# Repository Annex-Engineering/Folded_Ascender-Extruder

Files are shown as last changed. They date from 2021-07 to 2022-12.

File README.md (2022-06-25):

# Double Folded Ascender Extruder - Release "4"

Folded Ascender is a take on the "popular" worm direct-driven extruder system. It is available in a 20:1 variant.

The original concept was originally developed by Trails and RentableSocks back in ~March 2019, it has since evolved many times and RentableSocks has now taken over development on this extruder full time.

Our discord server can be found here: 

Join me on Discord (https://discord.gg/MzTR3zE)

The BOM and Sourcing Guide for this product can be found here: https://docs.google.com/spreadsheets/d/1O3eyVuQ6M4F03MJSDs4Z71_XyNjXL5HFTZr1jsaAtRc/edit?usp=sharing

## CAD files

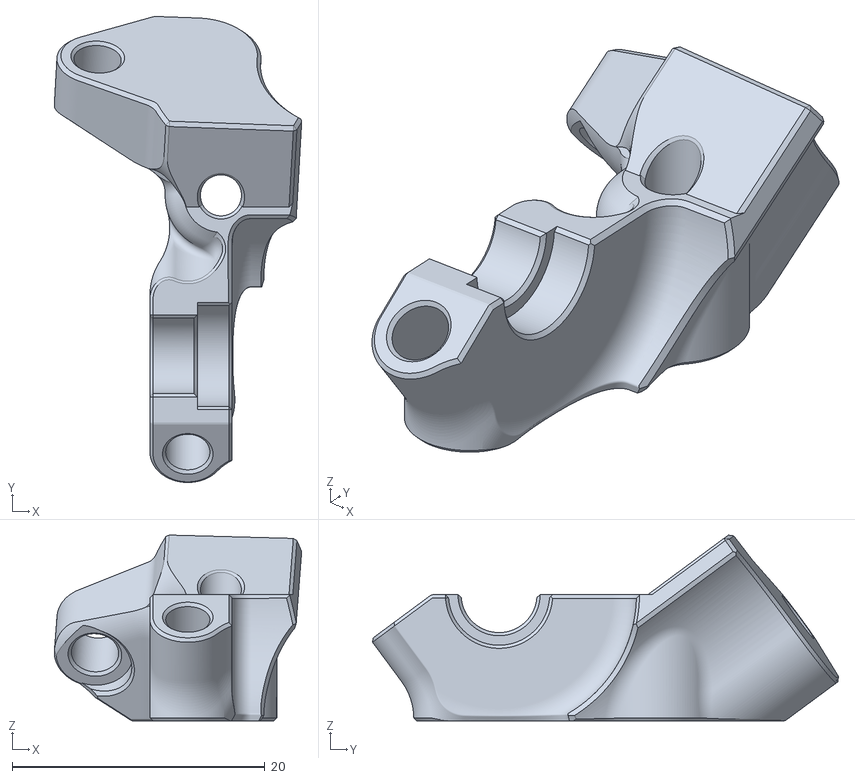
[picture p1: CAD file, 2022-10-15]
STLs/topcap_x1_rev2.stl
19.6 x 36.9 x 14.7

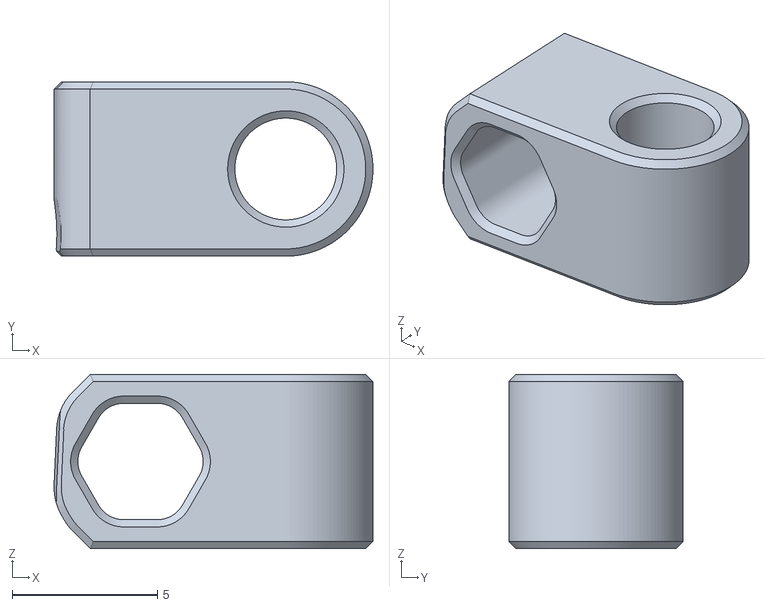
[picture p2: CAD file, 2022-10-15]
STLs/rev_bowden_dingus_x1_rev2.stl
11.0 x 6.00 x 6.00

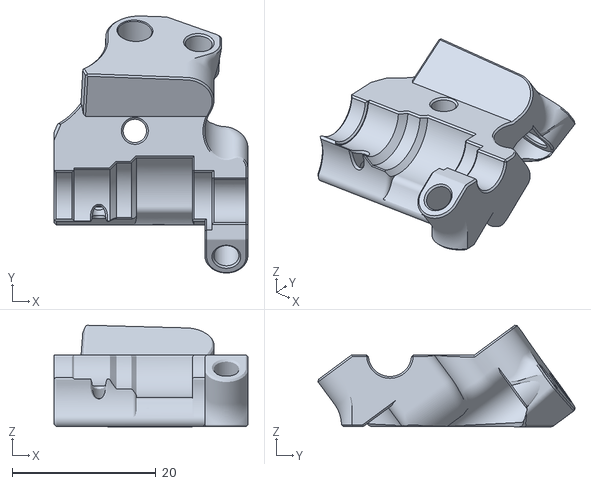
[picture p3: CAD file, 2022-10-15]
STLs/top_centered_x1_rev2.stl
27.0 x 35.8 x 14.1

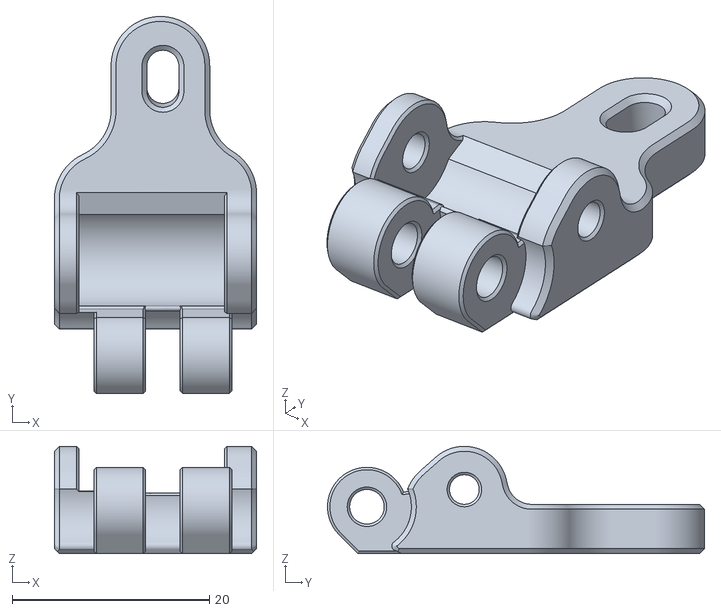
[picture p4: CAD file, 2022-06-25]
STLs/idlerlever_x1_rev1.stl
20.5 x 38.2 x 10.9

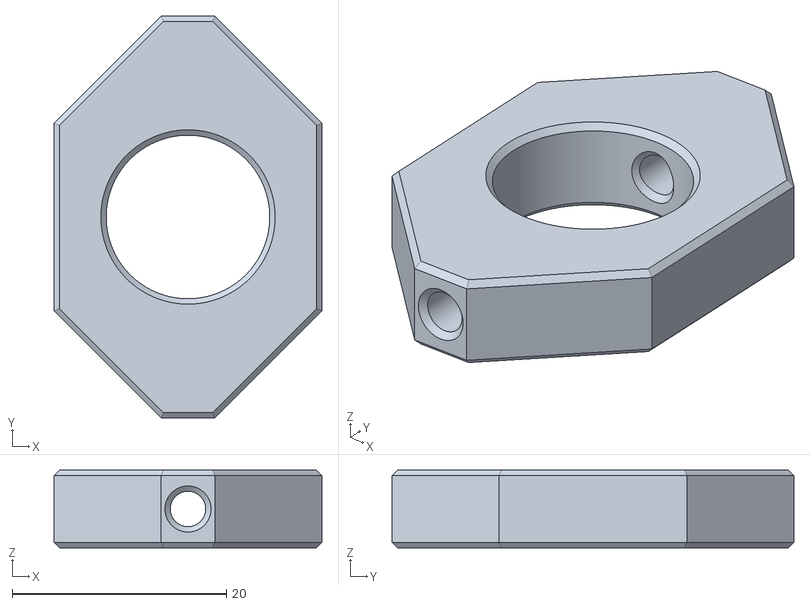
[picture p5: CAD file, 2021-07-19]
STLs/khk40t_set_screw_guide_x1_rev1.stl
25.0 x 37.5 x 7.25

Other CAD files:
CAD/Double_Folded_Ascender_R4p1.x_t

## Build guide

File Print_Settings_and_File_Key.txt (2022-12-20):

Primary Color: nothing at start of file name
Accent Color: [a]_ at start of file name
Quantity Required: _x# near end of file name
File Revision: _Rev# at end of file name

Nozzle Size: 0.5mm 
Recommended FDM Materials: ASA, Polymaker or 3DXTech Recommended
Alternate Approved FDM Materials: PC, 3DXTech Recommended
Layer Height: 0.15mm
Extrusion Width: Forced 0.5mm
Infill Percentage: 80% minimum (at 0.8mm Width)
Infill Type: Grid, Gyroid, Honeycomb, Triangle or Cubic
Wall Count: 3 minimum (at 0.5mm Width)
Solid Top/Bottom Layers: 6 minimum (at 0.15mm Height)

Nozzle Size: 0.4mm 
Recommended FDM Materials: ASA, Polymaker or 3DXTech Recommended
Alternate Approved FDM Materials: PC, 3DXTech Recommended
Layer Height: 0.15mm
Extrusion Width: Forced 0.4mm
Infill Percentage: 80% minimum (at 0.6mm Width)
Infill Type: Grid, Gyroid, Honeycomb, Triangle or Cubic
Wall Count: 4 minimum (at 0.4mm Width)
Solid Top/Bottom Layers: 6 minimum (at 0.15mm Height)

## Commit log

2020-02-02 prep for release
    prep for release
    [Klipper_Config_Block.txt, [a]_40to1_brass_spacer_x1_rev2.STL, [a]_bmg_gear_tensioning_arm_x1_Rev3.STL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]
2020-02-02 re-orient voron toolhead parts to proper print orientation
    [v6_holder_front_ascender_Rev3.STL]
2020-02-02 add super hacky but functional optional bowden tube retaining bracket
    this is by far not required, just makes loading easier if you have a large printer
    [[a]_optional_bowden_retaining_bracket_x1_rev1.STL]
2020-02-03 add 40mm VORON Universal Toolhead Parts, Reinforce Bowden Tube Mount
    add 40mm VORON Universal Toolhead Parts, Reinforce Bowden Tube Mount
    [[a]_optional_bowden_retaining_bracket_x1_rev1.STL, [a]_optional_bowden_retaining_bracket_x1_rev2.STL, [a]_toolhead_front_plate_30mm_rev2.STL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]
2020-02-05 alpha2 parts
    [[a]_40to1_brass_spacer_long_x1_rev3.STL, [a]_40to1_brass_spacer_short_x1_rev1.STL, [a]_bmg_gear_tensioning_arm_x1_Rev3.STL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]
2020-02-05 move bolt so motor can actually slide forwards
    move bolt so motor can actually slide forwards
    [housing_bottom_x1_rev4.STL, housing_bottom_x1_rev5.STL, housing_top_x1_rev4.STL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]
2020-02-06 alpha3 prep
    [[a]_40to1_brass_spacer_long_x1_rev3.STL, [a]_40to1_brass_spacer_short_x1_rev1.STL, [a]_bmg_gear_tensioning_arm_x1_Rev3.STL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]
2020-02-07 Update Klipper_Config_Block.txt
    update to latest tested numbers from 2 printers
    [Klipper_Config_Block.txt]
2020-02-07 beta 1
    [[a]_40to1_brass_spacer_long_x1_rev3.STL, [a]_40to1_brass_spacer_short_x1_rev1.STL, [a]_bmg_gear_tensioning_arm_x1_Rev4.STL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]
2020-02-08 add mosquito (30mm fan only) variant of toolhead parts
    add mosquito (30mm fan only) variant of toolhead parts
    [mosquito_holder_front_ascender_30mm_Rev1.STL, mosquito_holder_rear_ascender_Rev1.STL]
2020-02-09 update comment block in klipper config
    update comment block in klipper config
    [Klipper_Config_Block.txt]
2020-02-13 update retraction settings to most recient tested ones
    [Klipper_Config_Block.txt]
2020-02-15 beta3
    beta3
    [[a]_40to1_brass_spacer_long_x1_rev3.STL, [a]_40to1_brass_spacer_short_x1_rev1.STL, [a]_bmg_gear_tensioning_arm_x1_Rev6.STL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]
2020-02-25 beta5, add rentablesocks voron toolhead for 40mm v6
    [[a]_40to1_brass_spacer_long_x1_rev3.STL, [a]_40to1_brass_spacer_short_x1_rev1.STL, [a]_bmg_gear_tensioning_arm_x1_Rev7.STL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]
2020-02-25 add bridge lances to sides of top to hold wires
    add bridge lances to sides of top to hold wires
    [housing_top_x1_rev10.STL, housing_top_x1_rev11.STL]
2020-03-02 arm wasnt oriented correctly
    [[a]_bmg_gear_tensioning_arm_x1_Rev8.STL]
2020-03-05 flip part over
    [housing_top_x1_rev12.STL]
2020-03-07 update v6 toolheads to have better flow and cooling through heatsink, and more exhaust room
    update v6 toolheads to have better flow and cooling through heatsink, and more exhaust room
    [v6_holder_front_ascender_30mm_Rev4.STL, v6_holder_front_ascender_30mm_Rev5.STL, v6_holder_front_ascender_40mm_Rev2.STL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]
2020-03-10 add muni adapter
    [nimble_v1_mount_to_ascender.stl]
2020-03-14 release 2 - add official support for KHK gears
    release 2 - add official support for KHK gears
    [30to1_gear_hand_tap_setscrew_threads_x1_rev1.STL, [a]_40to1_spacer_long_x1_rev3.STL, [a]_40to1_spacer_short_x1_rev1.STL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]
2020-03-15 Delete 30to1_gear_hand_tap_setscrew_threads_x1_rev1.STL
    Added by mistake, was never tested
    [30to1_gear_hand_tap_setscrew_threads_x1_rev1.STL]
2020-03-26 add recommended settings for current for KHK gearset
    [Klipper_Config_Block.txt]
2020-03-26 fix typo, missing comment info
    [Klipper_Config_Block.txt]
2020-03-28 add rentable 40mm mosquito toolhead
2020-05-06 add release2 folder
    [40to1_gear_hand_tap_setscrew_threads_x1_rev1.STL, 40to1_gear_x1_rev1.stl, [a]_40to1_spacer_long_x1_rev3.STL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]
2020-05-07 add beta1 of release3
    [[a]_40to1_spacer_long_x1_rev3.STL, [a]_40to1_spacer_short_x1_rev1.STL]
2020-05-07 add socks light toolhead for mosquito
    add socks light toolhead for mosquito
2020-07-30 Add folder for Ascender Dragon Toolhead
    add files
    [40mm Fan Adapter.STL]
2020-09-06 folded ascender alpha 1
    [40mm Fan Adapter.STL, 40to1_gear_hand_tap_setscrew_threads_x1_rev1.STL, 40to1_gear_x1_rev1.stl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]
2020-12-08 double folded ascender parts
    [Centered_Folded_Ascender_B1_40_china - Bottom_x1_Rev1.stl, Centered_Folded_Ascender_B1_40_china - Orphan Cap_x1_Rev1.stl, Centered_Folded_Ascender_B1_40_china 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]
2021-02-07 update config to use rotation distance
    [Klipper_Config_Block.txt]
2021-07-16 Add tap guide for khk40t from Rentable Socks
    [khk40t_set_screw_guide.stl]
2021-08-18 Update default step distance
    This step distance seems to be a better starting point. Also corrected default PA value
    [Klipper_Config_Block.txt]
2022-06-25 double folded, rev4
    [Centered_Folded_Ascender_B1_40_china - Bottom_x1_Rev1.stl, Centered_Folded_Ascender_B1_40_china - Orphan Cap_x1_Rev1.stl, Centered_Folded_Ascender_B1_40_china 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]
2022-10-15 Fix interference on bowden dingus, correct distance between motor mounting holes
    [rev_bowden_dingus_x1_rev1.stl, rev_bowden_dingus_x1_rev2.stl, top_centered_x1_rev1.stl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]
2023-10-27 migrate printer, extruder and board configs to an MIT licensed repo
    [Klipper_Config_Block.txt]
